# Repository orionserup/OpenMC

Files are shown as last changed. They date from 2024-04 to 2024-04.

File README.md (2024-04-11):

# OpenMC

OpenMC is an Open Source motor controller which serves as an interface between digital inputs and a motor driver interface

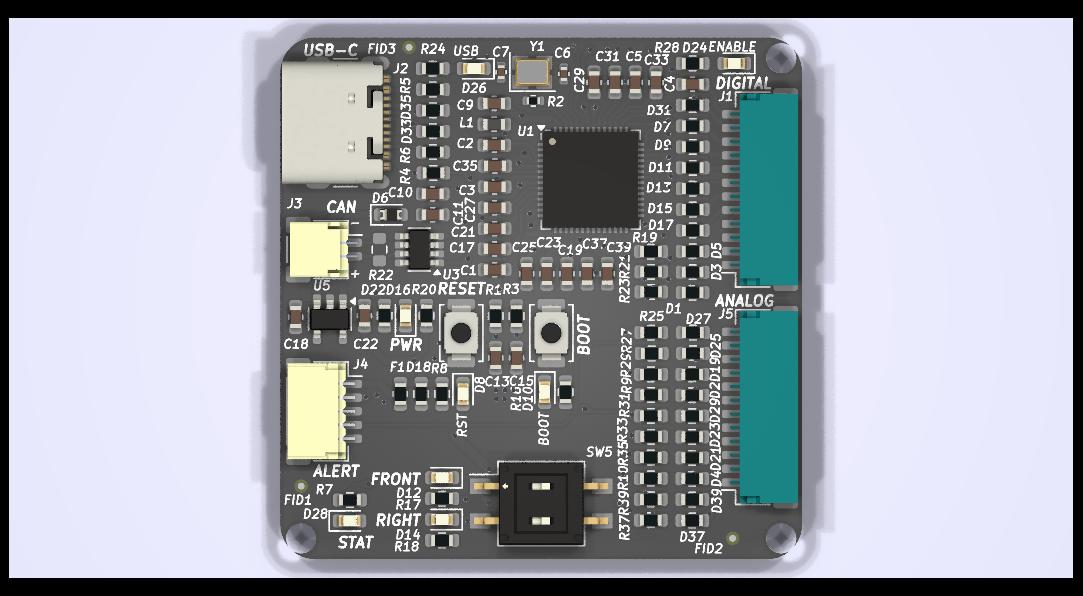
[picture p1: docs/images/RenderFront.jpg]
Front View

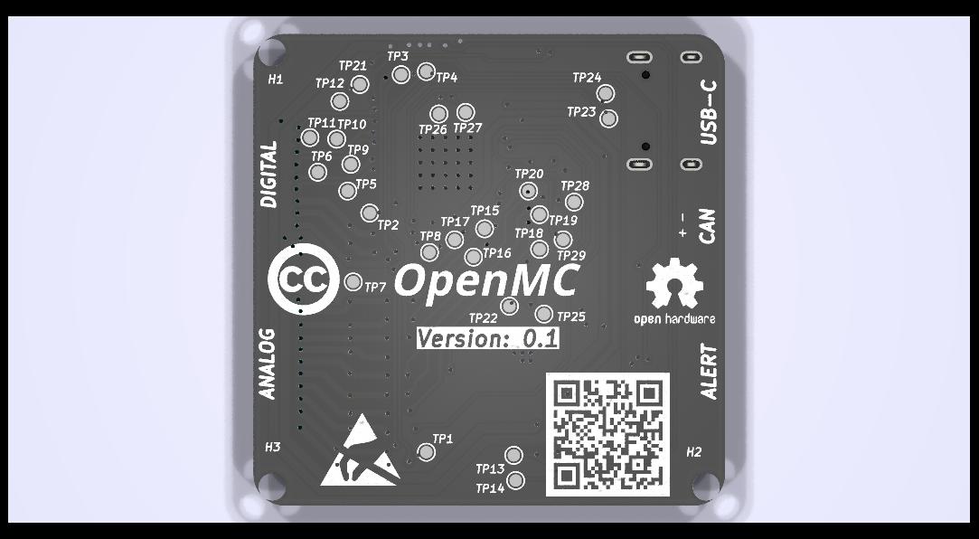
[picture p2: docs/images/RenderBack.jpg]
Back View


OpenMC is designed to be an affordable, flexible, scalable, and open solution to controller small scale electric vehicles (eBikes, Electric Scooters, eSk8, etc).

OpenMC is inspired by projects like [VESC](https://vesc-project.com/)

## Authors

[Orion Serup](mailto:oserup@proton.me)

## License

OpenMC is licensed under the [Creative Commons Share-Alike License](https://creativecommons.org/licenses/by-sa/4.0/)

All derivatives of this work must contain attribution to the original author as well as the same or similar license

This project can be used in any application without restriction (including commercial) provided that proper attribution and licensing terms are met

## Getting Started

Manufacturing files and compiled documentation can be directly downloaded through the releases tab by version.

If you want to modify the source or compile the documentation you will need the following dependencies

### Dependencies

OpenMC is designed using [KiCad](https://kicad.org) Version 8

The documentation is generated using [Typst](https://typst.app)

Version control and configuration management is done by Git and hosted on GitHub

### Downloading the Repository

The files can be downloaded from git, using the Github CLI, Github Desktop (or other visual Git tool) or directly from Github

[Repository Link](https://github.com/orionserup/OpenMC)

Download the repository by going to the GitHub and click on the Code button and select a method of download

## Building the Board

If you downloaded the source files you will have to generate manufacturing files of your own if you would like to build the board based on your local version. Reference KiCad manufacturing file export guides online for the process

Otherwise the generated manufacturing files can be used to build and assemble the board at just about any PCBA manufacturer

### Manufacturing the PCB

Submit the Gerber Files with drill files in zip form (Gerbers.zip if getting from releases) to your manufacturer of choice ([JLCPCB](https://jlcpcb.com) or [PCBWay](https://pcbway.com) is recommended)

The build parameters that are recommended are as follows, these settings will most likely yield the cheapest board with the fastest turn around time

- 1.6mm PCB Height (Not important but 1.6mm is standard)
- 2 Layer PCB
- 1 oz/ft^2 Copper Thickness (Can go down to .5 Oz/ft^2)
- HASL Surface Finish (Lead Free if you want but Leaded is fine)
- Green PCB Color (Official Build use Black but Green is Cheaper and Faster)
- White Silkscreen
- Tented Vias (Untented is also fine)
- No gold fingers, castellated holes, or edge plating

Any other parameters are likely not important and can be ignored

### Sourcing Parts

It is usually possible to have the PCB manufacturer source and purchase parts which are then assembled by them, we recommend doing this if you do not have the proper equipment to solder SMD components. Inquire with your manufacturer of choice to do this

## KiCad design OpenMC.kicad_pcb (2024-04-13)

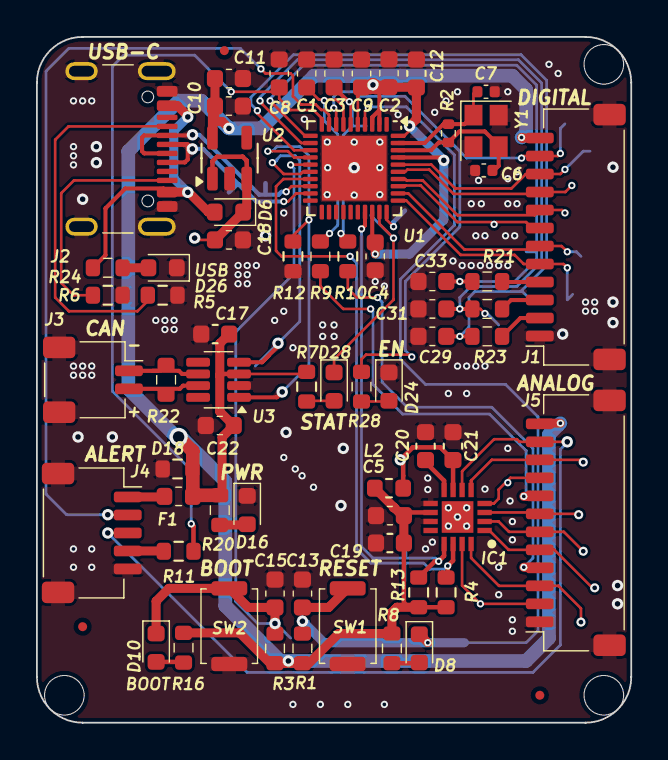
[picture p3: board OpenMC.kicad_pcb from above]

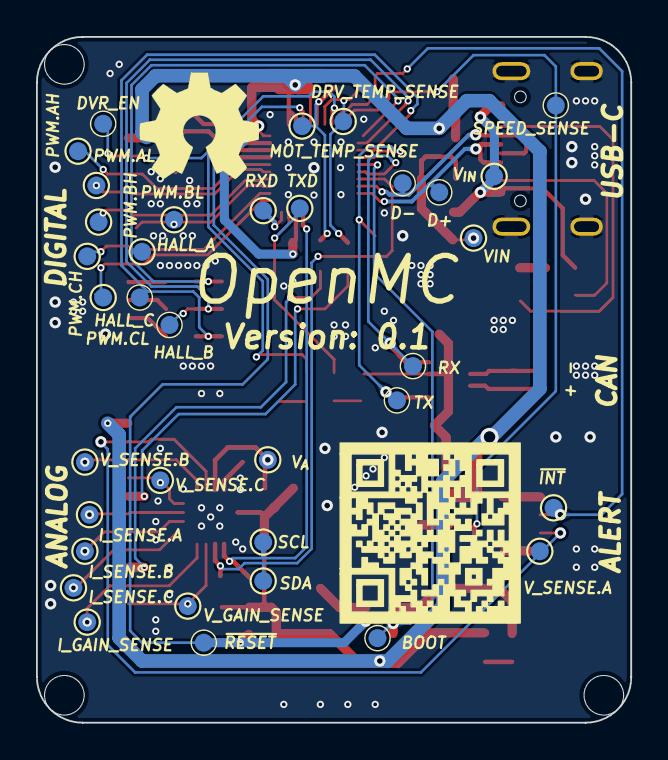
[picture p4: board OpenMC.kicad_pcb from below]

Board: 2 copper layers, 33.0 x 38.1 mm, 108 parts (39 on the bottom side), 57 nets.

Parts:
C1, C3, C5, C11, C13, C15, C19, C29, C31, C33: 100nF; C_0603_1608Metric
C2, C4, C8, C9, C10, C12, C17, C18, C21, C22: 4.7uF; C_0603_1608Metric
C6, C7: 10pF; C_0402_1005Metric
C20: 1uF; C_0603_1608Metric
D6: 430mV; D_0603_1608Metric
D8, D10, D16, D24: Red; LED_0603_1608Metric
D18: 10V; R_0603_1608Metric
D26, D28: Blue; LED_0603_1608Metric
F1: 1A; Fuse_0603_1608Metric
FID1, FID2, FID3: Fiducial; Fiducial_0.5mm_Mask1mm
H1, H2, H3: MountingHole; MountingHole_2.2mm_M2
IC1: TLA2528IRTER; QFN50P300X300X80-17N-D
J1: Motor Digital; JST_SH_SM12B-SRSS-TB_1x12-1MP_P1.00mm_Horizontal
J2: USB-C; USB_C_Receptacle_GCT_USB4105-xx-A_16P_TopMnt_Horizontal
J3: CAN; JST_SH_SM02B-SRSS-TB_1x02-1MP_P1.00mm_Horizontal
J4: Controller; JST_SH_SM05B-SRSS-TB_1x05-1MP_P1.00mm_Horizontal
J5: Motor Analog; JST_SH_SM12B-SRSS-TB_1x12-1MP_P1.00mm_Horizontal
L2: 1uH; L_0603_1608Metric
R1, R3, R7, R8, R9, R10, R11, R12, R16, R20, R24, R28: 4.7k; R_0603_1608Metric
R2: 1M; R_0402_1005Metric
R4, R13: 2.2k; R_0603_1608Metric
R5, R6: 5.1k; R_0603_1608Metric
R19, R21, R23: 10; R_0603_1608Metric
R22: 120; R_0603_1608Metric
SW1: RESET; SW_Push_SPST_NO_Alps_SKRK
SW2: BOOT; SW_Push_SPST_NO_Alps_SKRK
SYM1: Logo_Open_Hardware_Small; OSHW-Symbol_6.7x6mm_SilkScreen
TP1: MOT_TEMP_SENSE; TestPoint_Pad_D1.0mm
TP2: HALL_A; TestPoint_Pad_D1.0mm
TP3: HALL_B; TestPoint_Pad_D1.0mm
TP4: HALL_C; TestPoint_Pad_D1.0mm
TP5: PWM.CL; TestPoint_Pad_D1.0mm
TP6: PWM.CH; TestPoint_Pad_D1.0mm
TP7: DRV_TEMP_SENSE; TestPoint_Pad_D1.0mm
TP8: SPEED_SENSE; TestPoint_Pad_D1.0mm
TP9: PWM.BL; TestPoint_Pad_D1.0mm
TP10: PWM.BH; TestPoint_Pad_D1.0mm
TP11: PWM.AL; TestPoint_Pad_D1.0mm
TP12: PWM.AH; TestPoint_Pad_D1.0mm
TP13: SDA; TestPoint_Pad_D1.0mm
TP14: SCL; TestPoint_Pad_D1.0mm
TP15: VIN; TestPoint_Pad_D1.0mm
TP16: V_{IN}; TestPoint_Pad_D1.0mm
TP17: I_SENSE.C; TestPoint_Pad_D1.0mm
TP18: I_SENSE.B; TestPoint_Pad_D1.0mm
TP19: I_SENSE.A; TestPoint_Pad_D1.0mm
TP20: V_SENSE.C; TestPoint_Pad_D1.0mm
TP21: DVR_EN; TestPoint_Pad_D1.0mm
TP22: BOOT; TestPoint_Pad_D1.0mm
TP23: D+; TestPoint_Pad_D1.0mm
TP24: D-; TestPoint_Pad_D1.0mm
TP25: ~{RESET}; TestPoint_Pad_D1.0mm
TP26: TXD; TestPoint_Pad_D1.0mm
TP27: RXD; TestPoint_Pad_D1.0mm
TP28: RX; TestPoint_Pad_D1.0mm
TP29: TX; TestPoint_Pad_D1.0mm
TP30: V_SENSE.B; TestPoint_Pad_D1.0mm
TP31: V_SENSE.A; TestPoint_Pad_D1.0mm
TP32: V_{A}; TestPoint_Pad_D1.0mm
TP33: V_GAIN_SENSE; TestPoint_Pad_D1.0mm
TP34: I_GAIN_SENSE; TestPoint_Pad_D1.0mm
TP35: ~{INT}; TestPoint_Pad_D1.0mm
U1: ESP32-C6; QFN-40-1EP_5x5mm_P0.4mm_EP3.6x3.6mm
U2: AP2204K-3.3; SOT-23-5
U3: TCAN334; SOT-23-8
Y1: 40MHz; Crystal_SMD_2520-4Pin_2.5x2.0mm

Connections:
/3 Volt Supply/VIN: C18.1, D6.1 (K), TP15.1, U2.1 (VIN), U2.3 (EN)
/ADC/V_{A}: C21.1, IC1.7 (AVDD), L2.2, TP32.1
/AH: J1.10, TP12.1, U1.36 (GPIO23/SDIO_DATA3)
/AL: J1.9, TP11.1, U1.35 (GPIO22/SDIO_DATA2)
/BH: J1.8, TP10.1, U1.34 (GPIO21/SDIO_DATA1/FSPICS5)
/BL: J1.7, TP9.1, U1.33 (GPIO20/SDIO_DATA0/FSPICS4)
/CAN+: J3.2, R22.1, U3.7 (CANH)
/CAN-: J3.1, R22.2, U3.6 (CANL)
/CH: J1.6, TP6.1, U1.32 (GPIO19/SDIO_CLK/FSPICS3)
/CL: J1.5, TP5.1, U1.31 (GPIO18/SDIO_CMD/FSPICS2)
/D+: J2.A6 (D+), J2.B6 (D+), TP23.1, U1.19 (GPIO13/USB_D+)
/D-: J2.A7 (D-), J2.B7 (D-), TP24.1, U1.18 (GPIO12/USB_D-)
/DRIVER_TEMP_SENSE: J5.8, R9.2
/DRV_EN: J1.11, R28.1, TP21.1, U1.8 (GPIO2/FSPIQ/ADC1_CH2)
/GND: C1.2, C2.2, C3.2, C4.2, C5.2, C6.1, C7.1, C8.2, C9.2, C10.2, C11.2, C12.2, C13.2, C15.2, C17.2, C18.2, C19.2, C20.2, C21.2, C22.2, C29.2, C31.2, C33.2, D16.1 (K), D18.1 (A1), D24.1 (K), D26.1 (K), IC1.9 (GND), IC1.11 (ADDR), IC1.17 (EP), J1.1, J1.MP (MountPin), J2.A1 (GND), J2.A12 (GND), J2.B1 (GND), J2.B12 (GND), J2.S1 (SHIELD), J3.MP (MountPin), J4.5, J4.MP (MountPin), J5.1, J5.MP (MountPin), R5.1, R6.1, R12.2, SW1.1 (A), SW2.1 (A), U1.41 (GND), U2.2 (GND), U3.2 (GND), Y1.2, Y1.4
/HALL.A: J1.4, R19.1
/HALL.B: J1.3, R21.1
/HALL.C: J1.2, R23.1
/IGAIN_SENSE: IC1.16 (AIN1/GPIO1), J5.3, TP34.1
/I_SENSE.A: IC1.3 (AIN4/GPIO4), J5.7, TP19.1
/I_SENSE.B: IC1.2 (AIN3/GPIO3), J5.6, TP18.1
/I_SENSE.C: IC1.1 (AIN2/GPIO2), J5.5, TP17.1
/MOTOR_TEMP_SENSE: J5.4, R10.2
/Motor Controller /BOOT: C15.1, D10.1 (K), R3.1, SW2.2 (B), TP22.1, U1.15 (GPIO9)
/Motor Controller /DRV_TEMP_SENSE: C1.1, R9.1, TP7.1, U1.7 (GPIO1/XTAL_32K_N/ADC1_CH1)
/Motor Controller /HALL_A: C33.1, R19.2, TP2.1, U1.11 (MTDI/GPIO5/FSPIWP/ADC1_CH5)
/Motor Controller /HALL_B: C31.1, R21.2, TP3.1, U1.12 (MTCK/GPIO6/FSPICLK/ADC1_CH6)
/Motor Controller /HALL_C: C29.1, R23.2, TP4.1, U1.13 (MTDO/GPIO7/FSPID)
/Motor Controller /MOT_TEMP_SENSE: C3.1, R10.1, TP1.1, U1.6 (GPIO0/XTAL_32K_P/ADC1_CH0)
/Motor Controller /RXD: TP27.1, U1.30 (U0RXD/GPIO17/FSPICS1)
/Motor Controller /SPEED_SENSE: C8.1, R11.1, TP8.1, U1.10 (MTMS/GPIO4/FSPIHD/ADC1_CH4)
/Motor Controller /TXD: D28.1 (K), TP26.1, U1.29 (U0TXD/GPIO16/FSPICS0)
/Motor Controller /V_{DD}: C2.1, C4.1, C5.1, C9.1, C10.1, C11.1, C12.1, C17.1, C19.1, C22.1, D18.2 (A2), F1.1, IC1.10 (DVDD), J1.12, J5.12, L2.1, R1.2, R3.2, R4.2, R7.2, R8.2, R13.2, R16.2, R20.1, U1.2 (VDDA3P3), U1.3 (VDDA3P3), U1.5 (VDDPST1), U1.28 (VDDPST2), U1.37 (VDDA1), U1.40 (VDDA2), U2.5 (VOUT), U3.3 (VCC)
/Motor Controller /X+: C7.2, R2.1, U1.39 (XTAL_P), Y1.1
/Motor Controller /X-: C6.2, R2.2, U1.38 (XTAL_N), Y1.3
/Motor Controller /~RESET: C13.1, D8.1 (K), R1.1, SW1.2 (B), TP25.1, U1.4 (CHIP_PU)
/RX: TP28.1, U1.16 (GPIO10), U3.4 (RXD)
/SCL: IC1.13 (SCL), R13.1, TP14.1, U1.27 (GPIO15)
/SDA: IC1.14 (SDA), R4.1, TP13.1, U1.17 (GPIO11)
/SPEED_CTRL_SENSE: J4.4, R11.2
/TX: R12.1, TP29.1, U1.14 (GPIO8), U3.1 (TXD)
/VGAIN_SENSE: IC1.15 (AIN0/GPIO0), J5.2, TP33.1
/V_SENSE.A: IC1.6 (AIN7/GPIO7), J4.3, J5.11, TP31.1
/V_SENSE.B: IC1.5 (AIN6/GPIO6), J5.10, TP30.1
/V_SENSE.C: IC1.4 (AIN5/GPIO5), J5.9, TP20.1
/V_{BUS}: D6.2 (A), J2.A4 (VBUS), J2.A9 (VBUS), J2.B4 (VBUS), J2.B9 (VBUS), R24.1, TP16.1
/~INT: J4.2, TP35.1, U1.9 (GPIO3/ADC1_CH3)
unnamed: D8.2 (A), R8.1
unnamed: D10.2 (A), R16.1
unnamed: D16.2 (A), R20.2
unnamed: D24.2 (A), R28.2
unnamed: D26.2 (A), R24.2
unnamed: D28.2 (A), R7.1
unnamed: C20.1, IC1.8 (DECAP)
unnamed: J2.A5 (CC1), R5.2
unnamed: J2.B5 (CC2), R6.2
unnamed: F1.2, J4.1

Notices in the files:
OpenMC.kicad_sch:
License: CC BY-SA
